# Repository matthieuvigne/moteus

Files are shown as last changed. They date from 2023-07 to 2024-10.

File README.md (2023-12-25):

# nautilus - a fork for moteus brushless servo driver

`nautilus` is a direct fork of moteus's driver with modified shape and interface to fit inside MyActuator's RMDX motors
(Mini-Cheatah like design), as a replacement of their driver. The main modifications are:

 - use an SPI interface instead of CAN
 - secondary SPI port for external encoder
 - usage of the `CSD88599` half-bridges instead of individual MOSFET to reduce the number of components
 - modified board shape and layout to fit inside the motor
 - the design is done using KiCad instead of Eagle

All new files are in the `nautilus` folder.

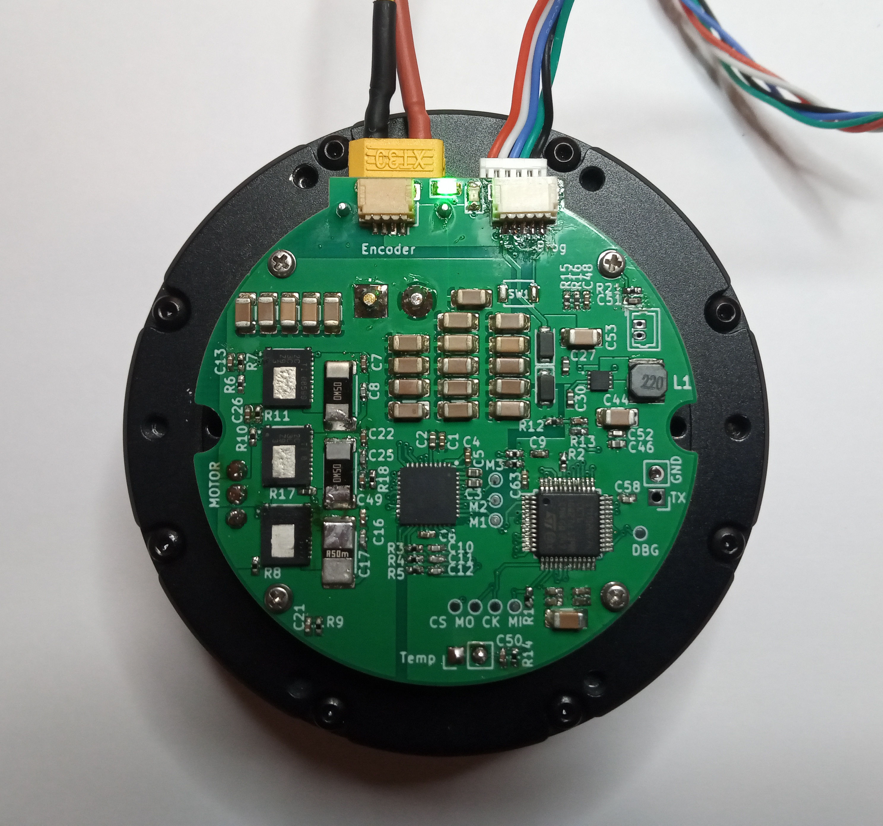
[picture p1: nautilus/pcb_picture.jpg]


# moteus brushless servo #

This contains full designs for the moteus brushless servo actuator,
including firmware and PCBs.

**WARNING**: This is not just a software project.  It includes designs
for moderately high power electronics.  It has not yet burned down my
(or anyone's that I know of) house, but there are no guarantees.

# Specifications #

| Name | Value |
|---|---|
| Voltage Input | 10-44V |
| Peak Electrical Power | 500W |
| Mass | 14.2g |
| Control Rate | 15-40kHz |
| PWM Switching Rate | 15-60kHz |
| CPU | 170Mhz STM32G4 |
| Peak phase current | 100A |
| Communications | 5Mbps CAN-FD |
| Dimensions | 46x53mm |

Assembled and tested boards can be purchased at https://mjbots.com/products/moteus-r4-11

# Directory structure #

* hw/ - hardware (mechanical and electrical designs)
  * controller/ - PCB design for servo controller
* fw/ - firmware for brushless controller
* lib/ - client side software
* utils/ - diagnostic tools
* tools/ - bazel build configure
* docs/ - documentation

# Documentation #

* [Getting Started](docs/getting_started.md)
* [Reference](docs/reference.md)

# Misc #

 * travis-ci 

# How to support moteus development #

The easiest way to support development the moteus hardware and firmware is as follows:

1) Buy things from https://mjbots.com
2) Build awesome machines!

That's it!  If for some reason you want to go above and beyond, you can sponsor mjbots through github: https://github.com/sponsors/mjbots

# License #

All files contained in this repository, unless otherwise noted, are
available under an Apache 2.0 License:
https://www.apache.org/licenses/LICENSE-2.0

# Trademark #

mjbots Robotic Systems LLC owns and protects the "mjbots" and "moteus" trademarks in many jurisdictions.

If you want to use these names in your project or product, please read the [Trademark Policy](https://mjbots.com/trademark-policy)

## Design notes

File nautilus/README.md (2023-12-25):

# How to compile and flash the firmware

## Installing dependencies

```sudo dnf install patch openocd arm-none-eabi-binutils-cs```

## Building the firmware

The firmware can be built by the following command:

```./tools/bazel test --config=target //fw:nautilus```

The bootloader also needs to be built (typically only once):

```./tools/bazel test --config=target //fw:can_bootloader ```

## Flashing

## Setting STM32 option bytes

Pin PB8 (boot) is used for I2C, thus pulled up. Hence, for the firmware to start running, the STM32 option bytes must be changed. This requires the software STM32CubeProgrammer, and the following configuration: nSWBOOT0 unchecked, nBOOT0 checked.

## Flashing

Simply run the python script: `python fw/flash.py`

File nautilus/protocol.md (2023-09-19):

# Nautilus motor driver protocol

Communication with the `nautilus` board is done using SPI. A fixed-size frame of 8 bytes is required for a complete transaction:

Input frame:
 - Byte 0: command byte 0
 - Byte 1: command byte 1 (typically register address)
 - Byte 2-5: data
 - Byte 6: unused
 - Byte 7: checksum

Output frame:
 - Byte 0-1: secondary encoder reading (14LSB) ; MSB 1 indicates a valid reading (Diagnostic register = 1)
 - Byte 2: current working mode
 - Byte 3-6: data
 - Byte 7: checksum

The checksum is simply the sum of the previous 6 bytes of the message.

**Note: for now, `nautilus` only supports SPI mode 1.**

## Available commands

### 0x01 <reg>: Register write

Write data to the register <reg>. If the register is non-writable, this has no effect

### 0x02 <reg>: Register read

Read data from register <reg>.

## 0x03: Perform commutation

For encoder commutation: enter voltage FOC mode:
 - next 4 bytes: float32_t, phase angle (0-1)
 - bytes 4-5: uint16_t, voltage amplitude as a fraction of maximum voltage

## 0x04 0x00: Store calibration results

Store the calibration result into persistent memory.

 - data[0-1]: uint16, encoder zero position
 - data[2]: uint8, encoder direction

## 0x05 0x00: Stop motor

## Register list

Address | Name                        | R/W | Persistent ? | Data type | Description
------- | ------------------          | --- | ------------ | --------- | -----------
0x00    | Current mode                | RO  | No           | uint8_t   | Current working mode, see details below
0x01    | Fault code                  | RO  | No           | uint32_t  | Fault error code

0x10    | Measured position           | RO  | No           | float32_t | Measured position, rad
0x11    | Measured speed              | RO  | No           | float32_t | Measured speed, rad/s
0x12    | Measured quadrature current | RO  | No           | float32_t | Measured quadrature current, A
0x13    | Measured current in phase A | RO  | No           | float32_t | Measured current in phase A, A
0x14    | Measured current in phase B | RO  | No           | float32_t | Measured current in phase B, A
0x15    | Measured current in phase C | RO  | No           | float32_t | Measured current in phase C, A
0x16    | Measured voltage in phase A | RO  | No           | float32_t | Measured voltage in phase A, V
0x17    | Measured voltage in phase B | RO  | No           | float32_t | Measured voltage in phase B, V
0x18    | Measured voltage in phase C | RO  | No           | float32_t | Measured voltage in phase C, V
0x19    | Measured motor temperature  | RO  | No           | float32_t | Measured motor temperature, C
0x1A    | Measured mosfet temperature | RO  | No           | float32_t | Measured mosfet temperature, C
0x1B    | Measured battery voltage    | RO  | No           | float32_t | Battery voltage, V

0x20    | Target position             | RW  | No           | float32_t | Target position, rad - also enter position mode
0x21    | Target speed                | RW  | No           | float32_t | Target speed, rad/s - also enter velocity mode
0x22    | Target quadrature current   | RW  | No           | float32_t | Target quadrature current, A - also enter current mode

0x30    | Raw encoder position        | RO  | No           | uint16_t | Raw encoder position, ticks
0x31    | Encoder orientation         | RW  | Yes          | uint8_t  | Encoder orientation with respect to motor
0x33    | Commutation offset          | RW  | Yes          | uint16_t | Commutation offset, ticks

0x40    | Current loop Kp             | RW  | Yes          | float32_t | Current loop Kp, V/A
0x41    | Current loop Ki             | RW  | Yes          | float32_t | Current loop Ki, Vs/A
0x42    | Current loop max integral   | RW  | Yes          | float32_t | Current loop max integral value, V

0x43    | Velocity loop Kp            | RW  | Yes          | float32_t | Velocity loop Kp, A/rad/s
0x44    | Velocity loop Ki            | RW  | Yes          | float32_t | Velocity loop Ki, As/rad/s
0x45    | Velocity loop max integral  | RW  | Yes          | float32_t | Velocity loop max integral value, A

0x50    | Motor max current           | RW  | Yes          | float32_t | Maximum motor current, A
0x51    | Motor max temperature       | RW  | Yes          | float32_t | Maximum motor temperature, deg C
0x52    | Mosfet max temperature      | RW  | Yes          | float32_t | Maximum mosfet temperature, deg C
0x53    | Communication timeout delay | RW  | Yes          | float32_t  | Communication timeout, s

## Register details

### 0x00: Current mode

Same as moteus:

    0 => stopped = writeable, clears faults
    1 => fault
    2,3,4 => preparing to operate
    5 => PWM mode
    6 => voltage mode
    7 => voltage FOC
    8 => voltage DQ
    9 => current
    10 => position
    11 => timeout
    12 => zero velocity
    13 => stay within
    14 => measure inductance
    15 => brake

 ### 0x01: Last error

Same as moteus 0x00f - fault code

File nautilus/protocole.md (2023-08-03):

# Nautilus motor driver protocole

Communication with the `nautilus` board is done using SPI. A fixed-size frame of 8 bytes is required for a
complete transaction:

Input frame:
 - Byte 0: command byte 0
 - Byte 1: command byte 1 (typically register address)
 - Byte 2-5: data
 - Byte 6: unused
 - Byte 7: checksum

Output frame:
 - Byte 0-1: secondary encoder reading
 - Byte 2: status byte
 - Byte 3-6: data
 - Byte 7: checksum

The checksum is simply the sum of the previous 6 bytes of the message.

## Available commands

### 0x01 <reg>: Register write

Write data to the register <reg>. If the register is non-writable, this has no effect

### 0x02 <reg>: Register read

Read data from register <reg>.

## 0x03 0x00: Perform calibration

Enter calibration mode: in voltage FOC, perform a full sweep of an electrical phase at the specified
velocity and power.

 - data[0-1]: uint16, duration of the sweep in ms.
 - data[2-3]: uint16, amplitude of the voltage in steps of 0.1%

## 0x03 0x01: Store calibration results

Store the calibration result into persistent memory.

## Register list

Address | Name                        | R/W | Persistent ? | Data type | Description
------- | ------------------          | --- | ------------ | --------- | -----------
0x00    | Current mode                | RW  | No           | uint32_t  | Current working mode, see details below
0x01    | Last error                  | RO  | No           | uint32_t  | Last error to have occured

0x10    | Measured position           | RO  | No           | float32_t | Measured position, rad
0x11    | Measured speed              | RO  | No           | float32_t | Measured speed, rad/s
0x12    | Measured quadrature current | RO  | No           | float32_t | Measured quadrature current, A
0x13    | Measured current in phase A | RO  | No           | float32_t | Measured current in phase A, A
0x14    | Measured current in phase B | RO  | No           | float32_t | Measured current in phase B, A
0x15    | Measured current in phase C | RO  | No           | float32_t | Measured current in phase C, A
0x16    | Measured voltage in phase A | RO  | No           | float32_t | Measured voltage in phase A, V
0x17    | Measured voltage in phase B | RO  | No           | float32_t | Measured voltage in phase B, V
0x18    | Measured voltage in phase C | RO  | No           | float32_t | Measured voltage in phase C, V
0x19    | Measured motor temperature  | RO  | No           | float32_t | Measured motor temperature, C
0x1A    | Measured mosfet temperature | RO  | No           | float32_t | Measured mosfet temperature, C
0x1B    | Measured battery voltage    | RO  | No           | float32_t | Battery voltage, V

0x20    | Target position             | RW  | No           | float32_t | Target position, rad
0x21    | Target speed                | RW  | No           | float32_t | Target speed, rad/s
0x22    | Target quadrature current   | RW  | No           | float32_t | Target quadrature current, A

0x30    | Raw encoder position        | RO  | No           | uint16_t | Raw encoder position, ticks
0x31    | Encoder orientation         | RW  | Yes          | uint8_t  | Encoder orientation with respect to motor
0x33    | Commutation offset          | RW  | Yes          | uint16_t | Commutation offset, ticks

0x40    | Current loop Kp             | RW  | Yes          | float32_t | Current loop Kp, V/A
0x41    | Current loop Ki             | RW  | Yes          | float32_t | Current loop Ki, Vs/A
0x42    | Current loop max integral   | RW  | Yes          | float32_t | Current loop max integral value, V

0x43    | Velocity loop Kp            | RW  | Yes          | float32_t | Velocity loop Kp, A/rad/s
0x44    | Velocity loop Ki            | RW  | Yes          | float32_t | Velocity loop Ki, As/rad/s
0x45    | Velocity loop max integral  | RW  | Yes          | float32_t | Velocity loop max integral value, A

0x50    | Motor max current           | RW  | Yes          | float32_t | Maximum motor current, A
0x51    | Motor max temperature       | RW  | Yes          | float32_t | Maximum motor temperature, deg C
0x52    | Mosfet max temperature      | RW  | Yes          | float32_t | Maximum mosfet temperature, deg C
0x53    | Communication timeout delay | RW  | Yes          | uint16_t  | Communication timeout limit, ms

## Register details

### 0x00: Current mode

List mode of operations:

 - 0x00: power off
 - 0x01: brake
 - 0x02: voltage FOC (commutation)
 - 0x03: current mode
 - 0x04: velocity mode

 ### 0x01: Last error

 List of errors: TODO

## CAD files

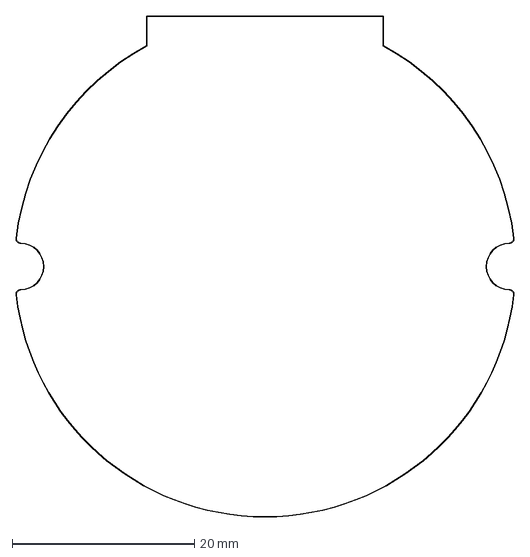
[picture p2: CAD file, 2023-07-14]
nautilus/hw/outline.dxf
54.7 x 55.0 mm

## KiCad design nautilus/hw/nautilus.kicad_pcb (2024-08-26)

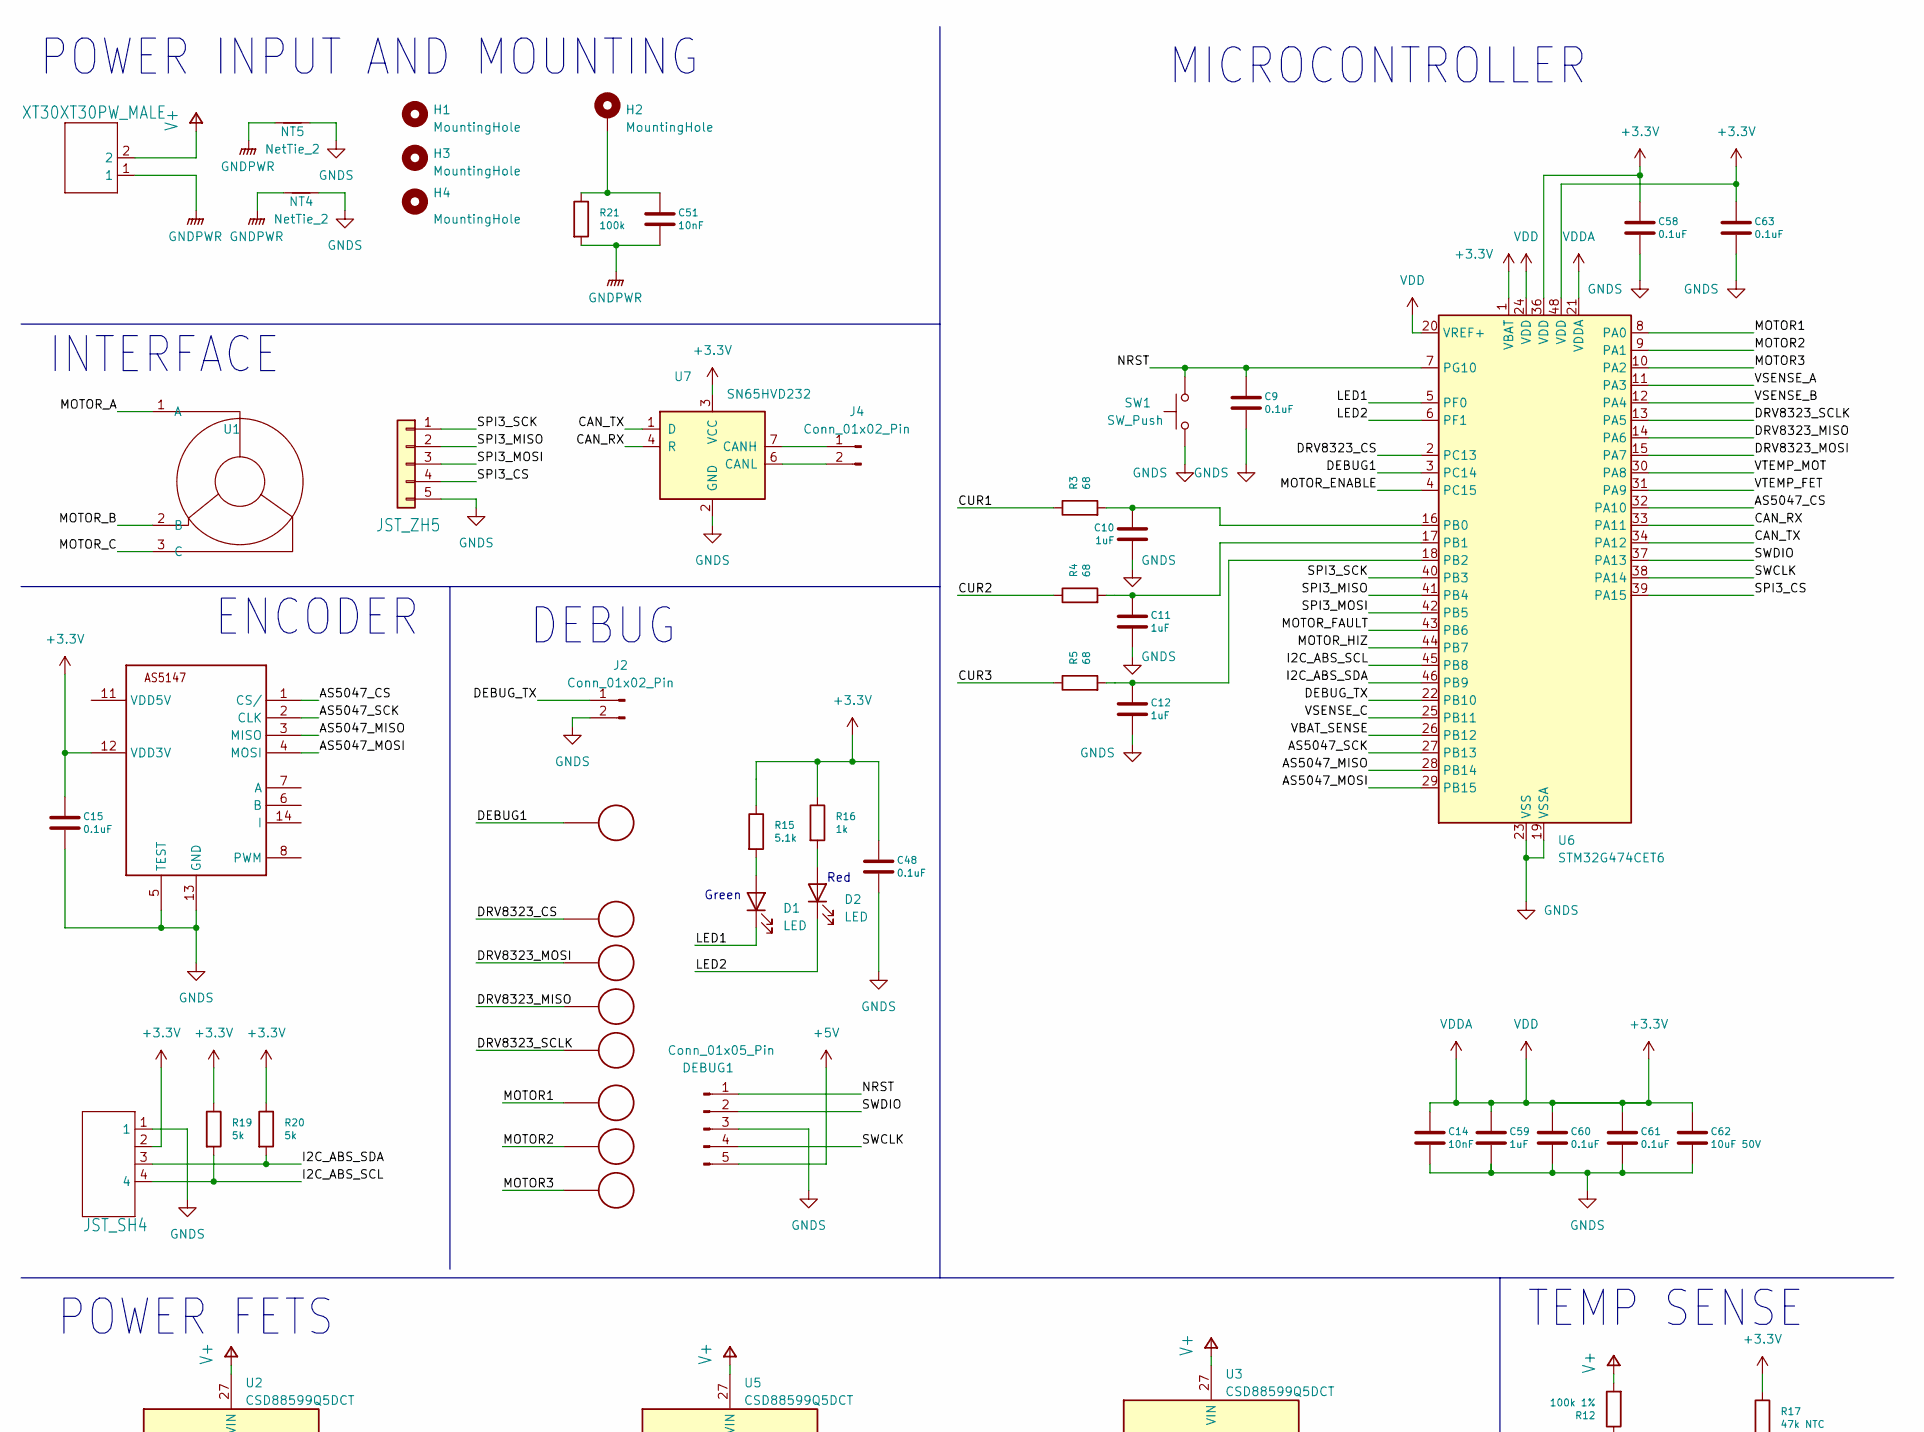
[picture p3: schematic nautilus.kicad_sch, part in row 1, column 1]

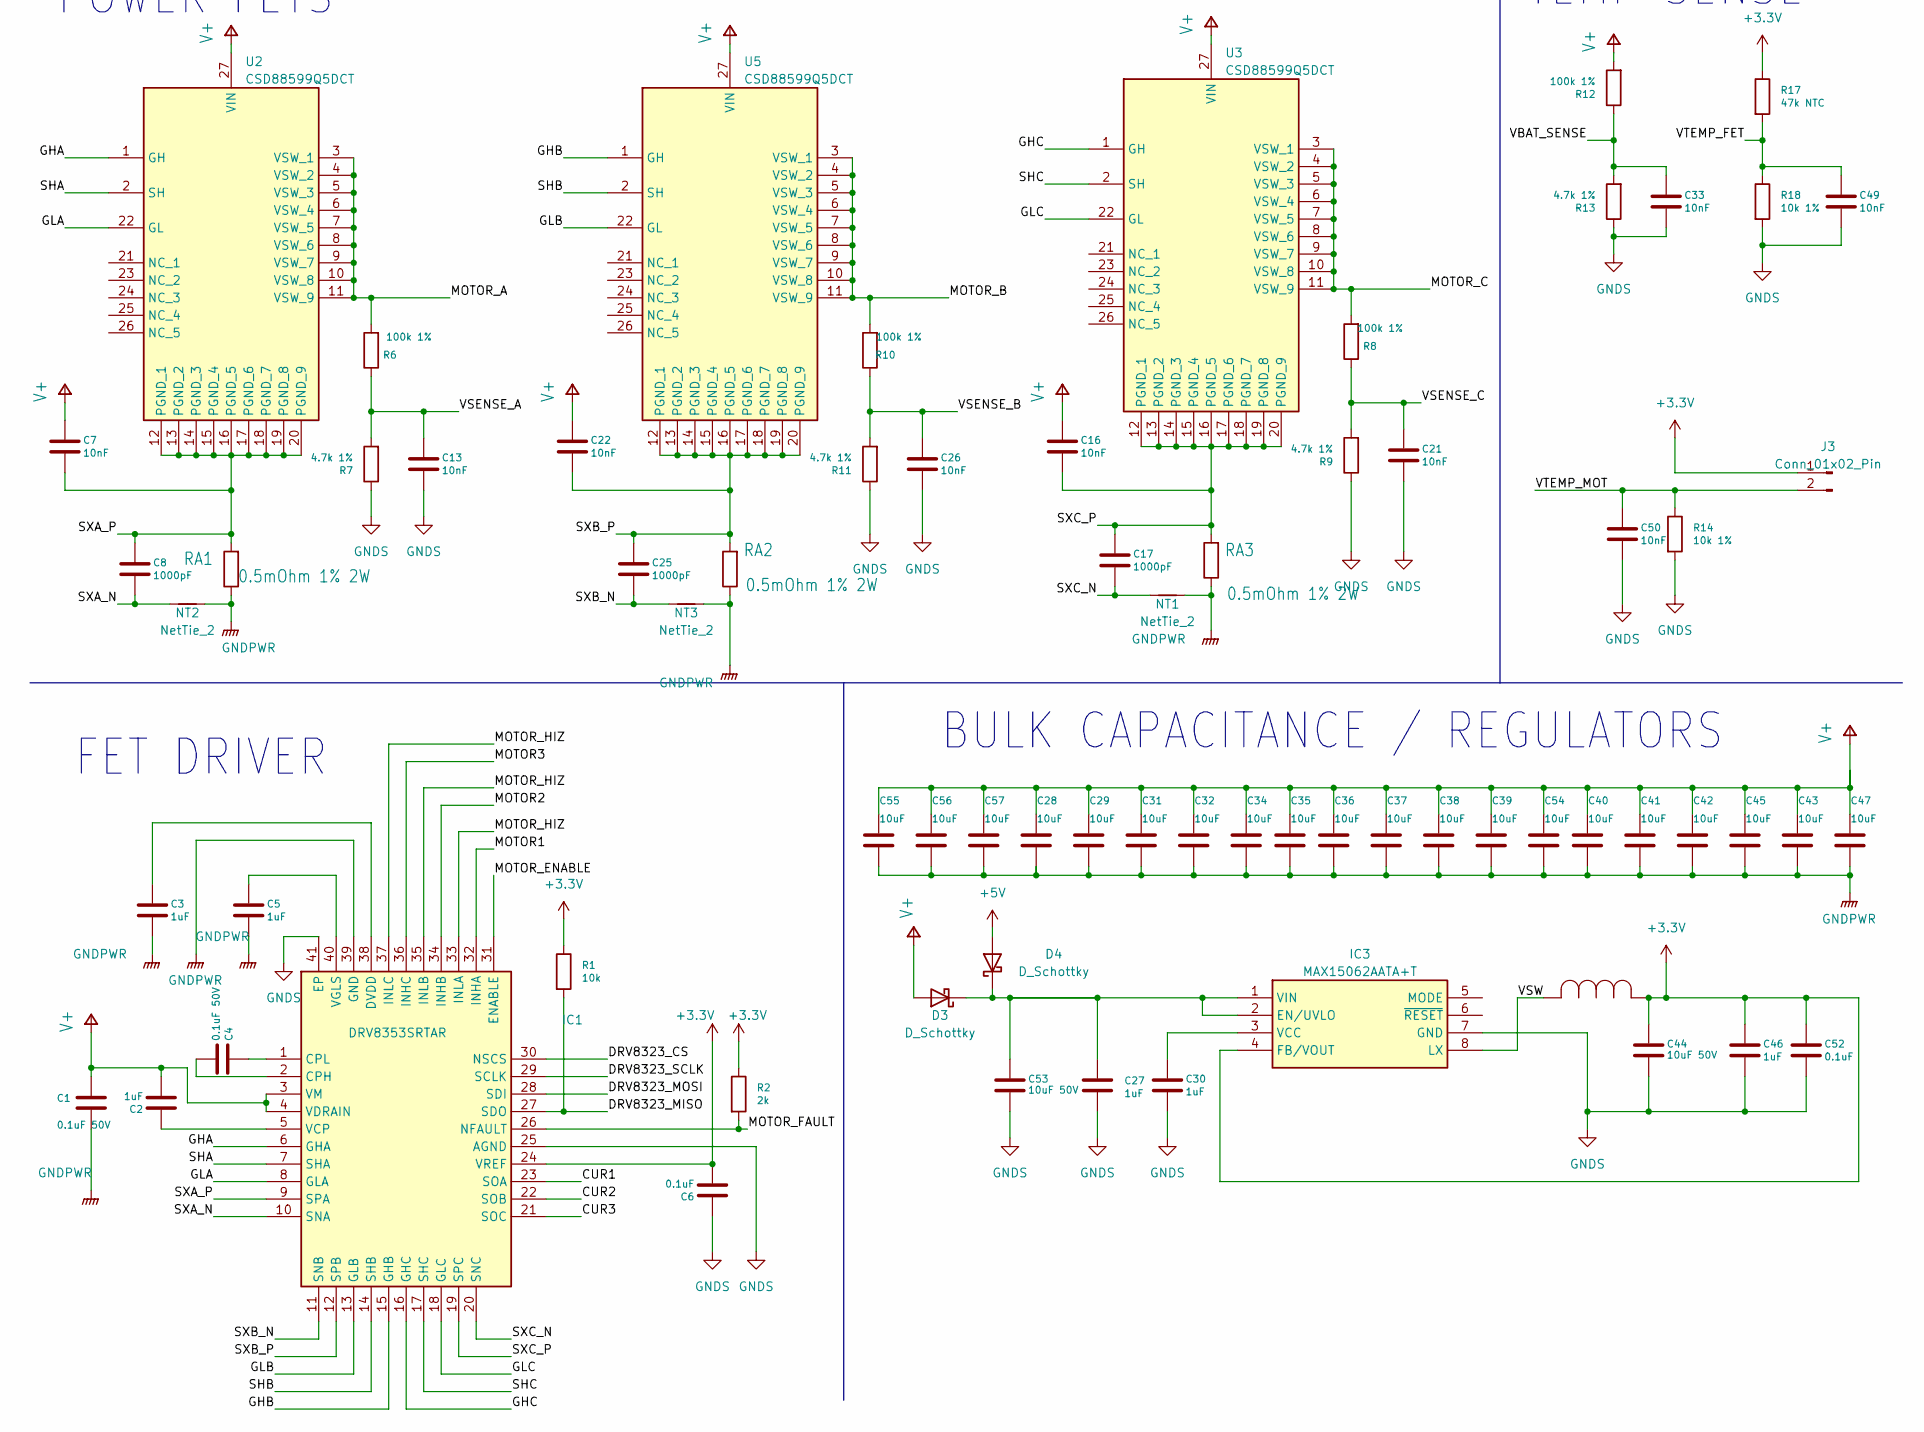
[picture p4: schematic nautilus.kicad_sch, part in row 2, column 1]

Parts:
C1, C4: 0.1uF 50V; C_0402_1005Metric_Pad0.74x0.62mm_HandSolder; MPN CGA2B3X7R1H104K050BB
C2, C3, C5, C46, C59: 1uF; C_0402_1005Metric_Pad0.74x0.62mm_HandSolder; MPN MF-CAP-0402-1uF
C6, C9, C15, C48, C52, C58, C60, C61, C63: 0.1uF; C_0402_1005Metric_Pad0.74x0.62mm_HandSolder; MPN MF-CAP-0402-0.1uF
C7, C13, C14, C16, C21, C22, C26, C51: 10nF; C_0402_1005Metric_Pad0.74x0.62mm_HandSolder; MPN MF-CAP-0402-1nF
C8, C17, C25: 1000pF; C_0402_1005Metric_Pad0.74x0.62mm_HandSolder; MPN MF-CAP-0402-1nF
C10, C11, C12: 1uF; C_0402_1005Metric_Pad0.74x0.62mm_HandSolder; MPN MF-CAP-0402-1nF
C27, C30: 1uF; C_0402_1005Metric_Pad0.74x0.62mm_HandSolder; MPN MF-CAP-0603-1uF
C28, C29, C31, C32, C34, C35, C36, C37, C38, C39, C40, C41, C42, C43, C45, C47, C54, C55, C56, C57: 10uF; C_1206_3216Metric_Pad1.33x1.80mm_HandSolder; MPN CL31A106MBHNNNE; Mouser Part Number 187-CL31A106MBHNNNE
C33, C50: 10nF; C_0402_1005Metric_Pad0.74x0.62mm_HandSolder; MPN MF-CAP-0402-0.01uF
C44, C53, C62: 10uF 50V; C_1206_3216Metric_Pad1.33x1.80mm_HandSolder; MPN CL31A106MBHNNNE; Mouser Part Number 187-CL31A106MBHNNNE
C49: 10nF; C_0402_1005Metric_Pad0.74x0.62mm_HandSolder; MPN MF-CAP-0402-0.1uF
D1, D2: LED; LED_0805_2012Metric_Pad1.15x1.40mm_HandSolder
D3, D4: D_Schottky; D_SOD-123F; Mouser Part Number 833-SMD210PLQ-TP
DBG1: PAD24AWG_PAD; TestPoint_Pad_D1.0mm
DEBUG1: Conn_01x05_Pin; JST_SH_SM05B-SRSS-TB_1x05-1MP_P1.00mm_Horizontal
DRV_CS1: PAD24AWG_PAD; TestPoint_Pad_D1.0mm
DRV_MISO1: PAD24AWG_PAD; TestPoint_Pad_D1.0mm
DRV_MOSI1: PAD24AWG_PAD; TestPoint_Pad_D1.0mm
DRV_SCK1: PAD24AWG_PAD; TestPoint_Pad_D1.0mm
H1, H2, H3, H4: MountingHole; MountingHole-Plated
IC1: DRV8353SRTAR; QFN50P600X600X80-41N-D; Manufacturer_Part_Number DRV8353SRTAR; Mouser Part Number 595-DRV8353SRTAT
IC3: MAX15062AATA+T; MAX15062AATAT; Manufacturer_Part_Number MAX15062AATA+T; Mouser Part Number 700-MAX15062AATA+T
J1: XT30XT30PW_MALE; AMASS_XT30PW-M_1x02_P2.50mm_Horizontal
J2, J3: Conn_01x02_Pin; PinHeader_1x02_P2.54mm_Vertical
J4: Conn_01x02_Pin; Molex_PicoBlade_53047-0210_1x02_P1.25mm_Vertical
L1: SRN4018-220M; SRN4018220M; MANUFACTURER_PART_NUMBER SRN4018-330M; Mouser SRN4018
M1, M2, M3: PAD24AWG_PAD; TestPoint_Pad_D1.0mm
NT1, NT2, NT3, NT4, NT5: NetTie_2; NetTie-2_SMD_Pad0.5mm
R1: 10k; R_0402_1005Metric_Pad0.72x0.64mm_HandSolder; MPN MF-RES-0402-2K
R2: 2k; R_0402_1005Metric_Pad0.72x0.64mm_HandSolder; MPN MF-RES-0402-2K
R3, R4, R5: 68; R_0402_1005Metric_Pad0.72x0.64mm_HandSolder; MPN MF-RES-0402-22
R6, R8, R10, R12: 100k 1%; R_0402_1005Metric_Pad0.72x0.64mm_HandSolder; MPN RC0402FR-07100KL
R7, R9, R11, R13: 4.7k 1%; R_0402_1005Metric_Pad0.72x0.64mm_HandSolder; MPN RC0402FR-074K7L
R14, R18: 10k 1%; R_0402_1005Metric_Pad0.72x0.64mm_HandSolder; MPN RC0402FR-0710KL
R15: 5.1k; R_0402_1005Metric_Pad0.72x0.64mm_HandSolder; MPN MF-RES-0402-560
R16: 1k; R_0402_1005Metric_Pad0.72x0.64mm_HandSolder; MPN MF-RES-0402-560
R17: 47k NTC; R_0402_1005Metric_Pad0.72x0.64mm_HandSolder; MPN NCP15WB473F03RC; Mouser Part Number 81-NCP15WB473F03RC
R19, R20: 5k; R_0402_1005Metric_Pad0.72x0.64mm_HandSolder; MPN MF-RES-0402-2K
R21: 100k; R_0402_1005Metric_Pad0.72x0.64mm_HandSolder; MPN MF-RES-0402-2K
RA1, RA2, RA3: 0.5mOhm 1% 2W; R_2512_6332Metric_Pad1.40x3.35mm_HandSolder; MPN HCS1206FTL500; Mouser 504-MSMA2512R0005FGM
SPI1: JST_ZH5; JST_GH_SM05B-GHS-TB_1x05-1MP_P1.25mm_Horizontal; MPN S4B-ZR-SM4A-TF(LF)(SN)
SPI2: JST_SH4; JST_SH_SM04B-SRSS-TB_1x04-1MP_P1.00mm_Horizontal; MPN S4B-ZR-SM4A-TF(LF)(SN)
SW1: SW_Push; SW_SPST_B3U-1000P
U1: BrushlessMotor
U2, U3, U5: CSD88599Q5DCT; Q5DC_DMM; Manufacturer_Part_Number CSD88599Q5DCT; Mouser Part Number 595-CSD88599Q5DCT
U4: AS5147; TSSOP-14_4.4x5mm_P0.65mm; MPN AS5047P-ATSM
U6: STM32G474CET6; LQFP-48_7x7mm_P0.5mm; Mouser Part Number 511-STM32G474CET6
U7: SN65HVD232; SOIC-8_3.9x4.9mm_P1.27mm

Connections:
+3.3V: C6.2, C14.1, C15.1, C44.1, C46.1, C48.1, C52.1, C58.1, C59.1, C60.1, C61.1, C62.1, C63.1, IC1.24 (VREF), IC3.4 (FB/VOUT), J3.1, L1.1, R1.1, R2.1, R15.1, R16.1, R17.1, R19.1, R20.1, SPI2.2, U4.12 (VDD3V), U6.1 (VBAT), U6.20 (VREF+), U6.21 (VDDA), U6.24 (VDD), U6.36 (VDD), U6.48 (VDD), U7.3 (VCC)
+5V: D4.2 (A), DEBUG1.5
/AS5047_CS: U4.1 (CS/), U6.32 (PA10)
/AS5047_MISO: U4.3 (MISO), U6.28 (PB14)
/AS5047_MOSI: U4.4 (MOSI), U6.29 (PB15)
/AS5047_SCK: U4.2 (CLK), U6.27 (PB13)
/CAN_RX: U6.33 (PA11), U7.4 (R)
/CAN_TX: U6.34 (PA12), U7.1 (D)
/CUR1: IC1.23 (SOA), R3.1
/CUR2: IC1.22 (SOB), R4.1
/CUR3: IC1.21 (SOC), R5.1
/DEBUG1: DBG1.1, U6.3 (PC14)
/DEBUG_TX: J2.1, U6.22 (PB10)
/DRV8323_CS: DRV_CS1.1, IC1.30 (NSCS), U6.2 (PC13)
/DRV8323_MISO: DRV_MISO1.1, IC1.27 (SDO), R1.2, U6.14 (PA6)
/DRV8323_MOSI: DRV_MOSI1.1, IC1.28 (SDI), U6.15 (PA7)
/DRV8323_SCLK: DRV_SCK1.1, IC1.29 (SCLK), U6.13 (PA5)
/GHA: IC1.6 (GHA), U2.1 (GH)
/GHB: IC1.15 (GHB), U5.1 (GH)
/GHC: IC1.16 (GHC), U3.1 (GH)
/GLA: IC1.8 (GLA), U2.22 (GL)
/GLB: IC1.13 (GLB), U5.22 (GL)
/GLC: IC1.18 (GLC), U3.22 (GL)
/I2C_ABS_SCL: R19.2, SPI2.4, U6.45 (PB8)
/I2C_ABS_SDA: R20.2, SPI2.3, U6.46 (PB9)
/LED1: D1.1 (K), U6.5 (PF0)
/LED2: D2.1 (K), U6.6 (PF1)
/MOTOR1: IC1.32 (INHA), M1.1, U6.8 (PA0)
/MOTOR2: IC1.34 (INHB), M2.1, U6.9 (PA1)
/MOTOR3: IC1.36 (INHC), M3.1, U6.10 (PA2)
/MOTOR_A: R6.2, U1.1 (A), U2.3 (VSW_1), U2.4 (VSW_2), U2.5 (VSW_3), U2.6 (VSW_4), U2.7 (VSW_5), U2.8 (VSW_6), U2.9 (VSW_7), U2.10 (VSW_8), U2.11 (VSW_9)
/MOTOR_B: R10.2, U1.2 (B), U5.3 (VSW_1), U5.4 (VSW_2), U5.5 (VSW_3), U5.6 (VSW_4), U5.7 (VSW_5), U5.8 (VSW_6), U5.9 (VSW_7), U5.10 (VSW_8), U5.11 (VSW_9)
/MOTOR_C: R8.2, U1.3 (C), U3.3 (VSW_1), U3.4 (VSW_2), U3.5 (VSW_3), U3.6 (VSW_4), U3.7 (VSW_5), U3.8 (VSW_6), U3.9 (VSW_7), U3.10 (VSW_8), U3.11 (VSW_9)
/MOTOR_ENABLE: IC1.31 (ENABLE), U6.4 (PC15)
/MOTOR_FAULT: IC1.26 (NFAULT), R2.2, U6.43 (PB6)
/MOTOR_HIZ: IC1.33 (INLA), IC1.35 (INLB), IC1.37 (INLC), U6.44 (PB7)
/NRST: C9.1, DEBUG1.1, SW1.2, U6.7 (PG10)
/SHA: IC1.7 (SHA), U2.2 (SH)
/SHB: IC1.14 (SHB), U5.2 (SH)
/SHC: IC1.17 (SHC), U3.2 (SH)
/SPI3_CS: SPI1.4, U6.39 (PA15)
/SPI3_MISO: SPI1.2, U6.41 (PB4)
/SPI3_MOSI: SPI1.3, U6.42 (PB5)
/SPI3_SCK: SPI1.1, U6.40 (PB3)
/SWCLK: DEBUG1.4, U6.38 (PA14)
/SWDIO: DEBUG1.2, U6.37 (PA13)
/SXA_N: C8.2, IC1.10 (SNA), NT2.2
/SXA_P: C7.2, C8.1, IC1.9 (SPA), RA1.2, U2.12 (PGND_1), U2.13 (PGND_2), U2.14 (PGND_3), U2.15 (PGND_4), U2.16 (PGND_5), U2.17 (PGND_6), U2.18 (PGND_7), U2.19 (PGND_8), U2.20 (PGND_9)
/SXB_N: C25.2, IC1.11 (SNB), NT3.2
/SXB_P: C22.2, C25.1, IC1.12 (SPB), RA2.2, U5.12 (PGND_1), U5.13 (PGND_2), U5.14 (PGND_3), U5.15 (PGND_4), U5.16 (PGND_5), U5.17 (PGND_6), U5.18 (PGND_7), U5.19 (PGND_8), U5.20 (PGND_9)
/SXC_N: C17.2, IC1.20 (SNC), NT1.2
/SXC_P: C16.2, C17.1, IC1.19 (SPC), RA3.2, U3.12 (PGND_1), U3.13 (PGND_2), U3.14 (PGND_3), U3.15 (PGND_4), U3.16 (PGND_5), U3.17 (PGND_6), U3.18 (PGND_7), U3.19 (PGND_8), U3.20 (PGND_9)
/VBAT_SENSE: C33.1, R12.1, R13.2, U6.26 (PB12)
/VSENSE_A: C13.1, R6.1, R7.2, U6.11 (PA3)
/VSENSE_B: C26.1, R10.1, R11.2, U6.12 (PA4)
/VSENSE_C: C21.1, R8.1, R9.2, U6.25 (PB11)
/VSW: IC3.8 (LX), L1.2
/VTEMP_FET: C49.1, R17.2, R18.1, U6.31 (PA9)
/VTEMP_MOT: C50.1, J3.2, R14.1, U6.30 (PA8)
GNDPWR: C1.2, C3.2, C5.2, C28.2, C29.2, C31.2, C32.2, C34.2, C35.2, C36.2, C37.2, C38.2, C39.2, C40.2, C41.2, C42.2, C43.2, C45.2, C47.2, C51.2, C54.2, C55.2, C56.2, C57.2, IC1.39 (GND), J1.1, NT1.1, NT2.1, NT3.1, NT4.2, NT5.2, R21.2, RA1.1, RA2.1, RA3.1
GNDS: C6.1, C9.2, C10.2, C11.2, C12.2, C13.2, C14.2, C15.2, C21.2, C26.2, C27.2, C30.2, C33.2, C44.2, C46.2, C48.2, C49.2, C50.2, C52.2, C53.2, C58.2, C59.2, C60.2, C61.2, C62.2, C63.2, DEBUG1.3, IC1.25 (AGND), IC1.41 (EP), IC3.7 (GND), J2.2, NT4.1, NT5.1, R7.1, R9.1, R11.1, R13.1, R14.2, R18.2, SPI1.5, SPI2.1, SW1.1, U4.5 (TEST), U4.13 (GND), U6.19 (VSSA), U6.23 (VSS), U6.35 (VSS), U6.47 (VSS), U7.2 (GND)
unnamed: C51.1, H2.1, R21.1
unnamed: D1.2 (A), R15.2
unnamed: D2.2 (A), R16.2
unnamed: C27.1, C53.1, D3.1 (K), D4.1 (K), IC3.1 (VIN), IC3.2 (EN/UVLO)
unnamed: C4.2, IC1.2 (CPH)
unnamed: C4.1, IC1.1 (CPL)
unnamed: C3.1, IC1.38 (DVDD)
unnamed: C2.1, IC1.5 (VCP)
unnamed: C5.1, IC1.40 (VGLS)
unnamed: C30.1, IC3.3 (VCC)
unnamed: J4.1, U7.7 (CANH)
unnamed: J4.2, U7.6 (CANL)
unnamed: C10.1, R3.2, U6.16 (PB0)
unnamed: C11.1, R4.2, U6.17 (PB1)
unnamed: C12.1, R5.2, U6.18 (PB2)
V+: C1.1, C2.2, C7.1, C16.1, C22.1, C28.1, C29.1, C31.1, C32.1, C34.1, C35.1, C36.1, C37.1, C38.1, C39.1, C40.1, C41.1, C42.1, C43.1, C45.1, C47.1, C54.1, C55.1, C56.1, C57.1, D3.2 (A), IC1.3 (VM), IC1.4 (VDRAIN), J1.2, R12.2, U2.27 (VIN), U3.27 (VIN), U5.27 (VIN)

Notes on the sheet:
Green
INTERFACE
POWER INPUT AND MOUNTING
TEMP SENSE
ENCODER
Red
MICROCONTROLLER
FET DRIVER
BULK CAPACITANCE / REGULATORS
DEBUG
POWER FETS

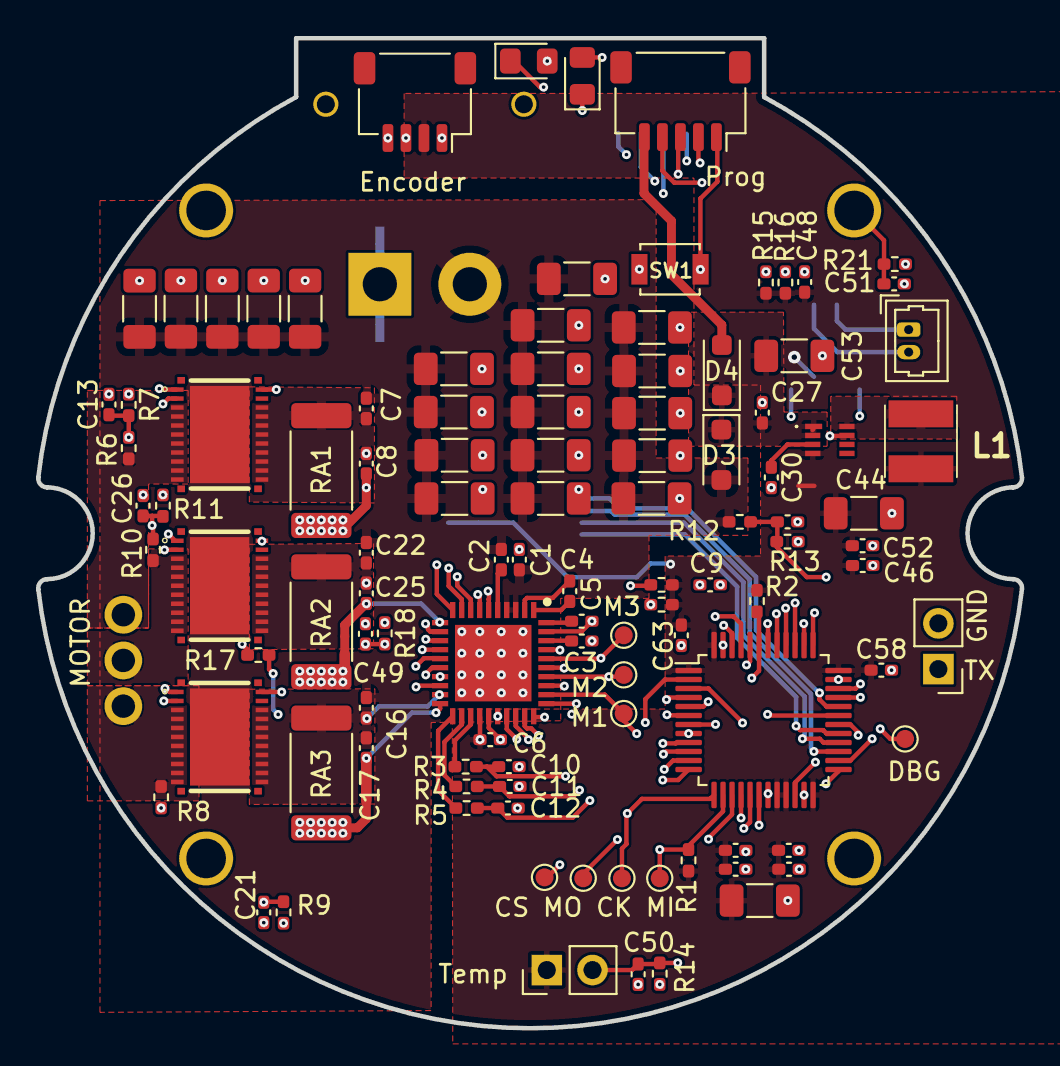
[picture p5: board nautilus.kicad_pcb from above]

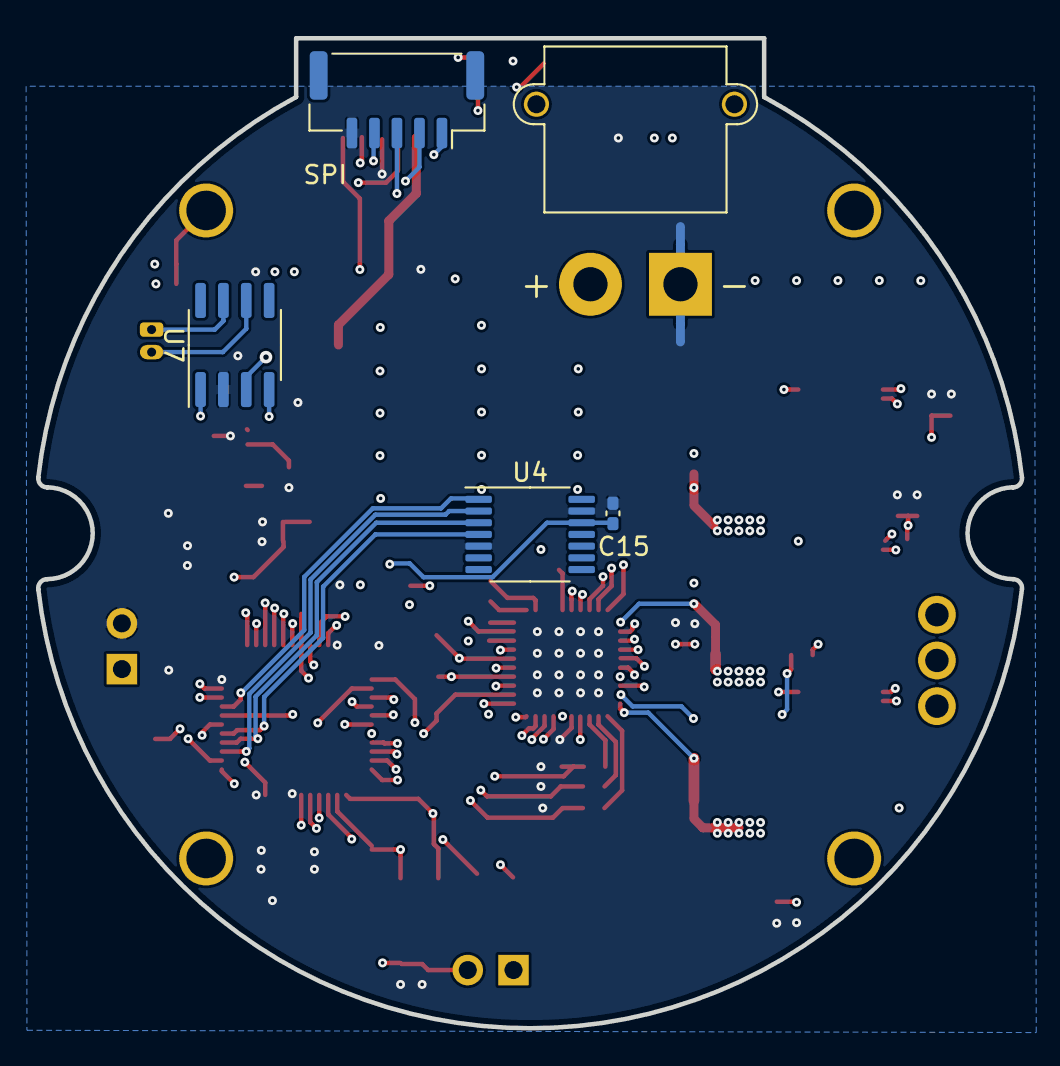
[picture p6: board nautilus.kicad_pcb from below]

Board: 4 copper layers, 54.7 x 55.0 mm, 121 parts (7 on the bottom side), 77 nets.

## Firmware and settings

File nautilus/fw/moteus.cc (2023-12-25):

// Copyright 2018-2022 Josh Pieper, jjp@pobox.com.
//
// Licensed under the Apache License, Version 2.0 (the "License");
// you may not use this file except in compliance with the License.
// You may obtain a copy of the License at
//
//     http://www.apache.org/licenses/LICENSE-2.0
//
// Unless required by applicable law or agreed to in writing, software
// distributed under the License is distributed on an "AS IS" BASIS,
// WITHOUT WARRANTIES OR CONDITIONS OF ANY KIND, either express or implied.
// See the License for the specific language governing permissions and
// limitations under the License.

#include <inttypes.h>

#include <functional>

#include "mbed.h"

#include "mjlib/micro/async_exclusive.h"
#include "mjlib/micro/async_stream.h"
#include "mjlib/micro/command_manager.h"
#include "mjlib/micro/persistent_config.h"
#include "mjlib/micro/telemetry_manager.h"
#include "mjlib/micro/stream_pipe.h"
#include "mjlib/multiplex/micro_server.h"
#include "mjlib/multiplex/micro_stream_datagram.h"

#include "fw/board_debug.h"
#include "fw/clock_manager.h"
#include "fw/firmware_info.h"
#include "fw/git_info.h"
#include "fw/millisecond_timer.h"
#include "fw/moteus_controller.h"
#include "fw/moteus_hw.h"
#include "fw/system_info.h"
#include "fw/uuid.h"

#if defined(TARGET_STM32G4)
#include "fw/fdcan.h"
#include "fw/fdcan_micro_server.h"
#include "fw/stm32g4_async_uart.h"
#include "fw/stm32g4_flash.h"
#else
#error "Unknown target"
#endif

extern "C" {
  uint32_t kMoteusFirmwareVersion = MOTEUS_FIRMWARE_VERSION;
}

auto* const MyDWT = DWT;
auto* const MyFLASH = FLASH;

using namespace moteus;
namespace micro = mjlib::micro;
namespace multiplex = mjlib::multiplex;

#if defined(TARGET_STM32G4)
using HardwareUart = Stm32G4AsyncUart;
using Stm32Flash = Stm32G4Flash;
#else
#error "Unknown target"
#endif

extern "C" {
void SetupClock() {
#if defined(TARGET_STM32G4)
  {
    __HAL_RCC_SYSCFG_CLK_ENABLE();
    __HAL_RCC_PWR_CLK_ENABLE();

    RCC_ClkInitTypeDef RCC_ClkInitStruct;

    RCC_ClkInitStruct.ClockType      = (RCC_CLOCKTYPE_SYSCLK | RCC_CLOCKTYPE_HCLK | RCC_CLOCKTYPE_PCLK1 | RCC_CLOCKTYPE_PCLK2);
    RCC_ClkInitStruct.SYSCLKSource = RCC_SYSCLKSOURCE_PLLCLK;
    RCC_ClkInitStruct.AHBCLKDivider = RCC_SYSCLK_DIV1; // 170 MHz
    RCC_ClkInitStruct.APB1CLKDivider = RCC_HCLK_DIV2;  //  85 MHz
    RCC_ClkInitStruct.APB2CLKDivider = RCC_HCLK_DIV2;  //  85 MHz

    if (HAL_RCC_ClockConfig(&RCC_ClkInitStruct, FLASH_LATENCY_6) != HAL_OK) {
      mbed_die();
    }

    RCC_PeriphCLKInitTypeDef PeriphClkInit = {};

    PeriphClkInit.PeriphClockSelection =
        RCC_PERIPHCLK_FDCAN |
        RCC_PERIPHCLK_USART2 |
        RCC_PERIPHCLK_USART3 |
        RCC_PERIPHCLK_ADC12 |
        RCC_PERIPHCLK_ADC345 |
        RCC_PERIPHCLK_I2C1
        ;
    PeriphClkInit.FdcanClockSelection = RCC_FDCANCLKSOURCE_PCLK1;
    PeriphClkInit.Usart2ClockSelection = RCC_USART2CLKSOURCE_PCLK1;
    PeriphClkInit.Usart3ClockSelection = RCC_USART3CLKSOURCE_PCLK1;
    PeriphClkInit.Adc12ClockSelection = RCC_ADC12CLKSOURCE_SYSCLK;
    PeriphClkInit.Adc345ClockSelection = RCC_ADC345CLKSOURCE_SYSCLK;
    PeriphClkInit.I2c1ClockSelection = RCC_I2C1CLKSOURCE_SYSCLK;
    if (HAL_RCCEx_PeriphCLKConfig(&PeriphClkInit) != HAL_OK) {
      mbed_die();
    }

    __HAL_RCC_TIM2_CLK_ENABLE();
    __HAL_RCC_TIM3_CLK_ENABLE();
    __HAL_RCC_TIM4_CLK_ENABLE();
  }
#endif
}
}

#if defined(TARGET_STM32G4)
extern "C" {
extern char _sccmram;
extern char _siccmram;
extern char _eccmram;
extern char _sccmram;
}
#endif

namespace moteus {
volatile uint8_t g_measured_hw_family;
volatile uint8_t g_measured_hw_rev;
volatile uint8_t g_measured_hw_pins;
MoteusHwPins g_hw_pins;
}

namespace {
struct CanConfig {
  uint32_t prefix = 0;

  template <typename Archive>
  void Serialize(Archive* a) {
    a->Visit(MJ_NVP(prefix));
  }

  bool operator==(const CanConfig& rhs) const {
    return prefix == rhs.prefix;
  }
};
}

int main(void) {
#if defined(TARGET_STM32G4)
  std::memcpy(&_sccmram, &_siccmram, &_eccmram - &_sccmram);
#endif

  FLASH->ACR |= FLASH_ACR_PRFTEN | FLASH_ACR_ICEN | FLASH_ACR_DCEN;

#if 0
  // We map SRAM1 onto address 0 just to make finding accesses to
  // address 0 easier.
  SYSCFG->MEMRMP = (SYSCFG->MEMRMP & ~SYSCFG_MEMRMP_MEM_MODE_Msk) | 0x03;  // SRAM1
#endif

  SetupClock();

  // I initially used a Ticker here to enqueue events at 1ms
  // intervals.  However, it introduced jitter into the current
  // sampling interrupt, and I couldn't figure out how to get the
  // interrupt priorities right.  Thus for now we just poll to look
  // for millisecond turnover.
  MillisecondTimer timer;

  const auto family_and_version = DetectMoteusFamily(&timer);
  g_measured_hw_family = family_and_version.family;
  g_measured_hw_rev = family_and_version.hw_version;
  g_measured_hw_pins = family_and_version.hw_pins;

  g_hw_pins = FindHardwarePins(family_and_version);

  // We do our compatibility check *after* calling FindHardwarePins so
  // the the family specific pins are known.  That way mbed_die
  // doesn't choke being unable to find the power LED for instance.

  if (family_and_version.hw_version < 0) {
    // This firmware is not compatible with this board.
    mbed_die();
  }

  // We require cycle counting be enabled for some things.
  {
    ITM->LAR = 0xC5ACCE55;
    CoreDebug->DEMCR |= CoreDebug_DEMCR_TRCENA_Msk;
    DWT->CYCCNT = 0;
    DWT->CTRL |= DWT_CTRL_CYCCNTENA_Msk;
  }

  micro::SizedPool<20000> pool;

  std::optional<HardwareUart> rs485;
  if (g_hw_pins.uart_tx != NC) {
    rs485.emplace(&pool, &timer, []() {
      HardwareUart::Options options;
      options.tx = g_hw_pins.uart_tx;
      options.rx = g_hw_pins.uart_rx;
      options.dir = g_hw_pins.uart_dir;
      options.baud_rate = 1000000;
      return options;
                                 }());
  }

  FDCan fdcan([]() {
      FDCan::Options options;

      options.td = g_hw_pins.can_td;
      options.rd = g_hw_pins.can_rd;

      options.slow_bitrate = 1000000;
      options.fast_bitrate = 5000000;

      options.fdcan_frame = true;
      options.bitrate_switch = true;
      options.automatic_retransmission = true;

      // Family 0 uses a TCAN334GDCNT, which has a very low loop
      // delay.  Other families use chips with a longer loop delay.
      options.delay_compensation = g_measured_hw_family != 0;

      options.tdc_offset = 13;  // 13 / 85MHz ~= 152ns
      options.tdc_filter = 2; // 2 / 85MHz ~= 23ns

      return options;
    }());
  FDCanMicroServer fdcan_micro_server(&fdcan);
  multiplex::MicroServer multiplex_protocol(
      &pool, &fdcan_micro_server,
      []() {
        multiplex::MicroServer::Options options;
        options.max_tunnel_streams = 3;
        return options;
      }());

  // micro::AsyncStream* serial = multiplex_protocol.MakeTunnel(1);

  // micro::AsyncExclusive<micro::AsyncWriteStream> write_stream(serial);

  micro::EventQueue event_queue;
  micro::StreamPipe pipe{event_queue.MakePoster()};
  micro::AsyncExclusive<micro::AsyncWriteStream> write_stream{pipe.side_a()};

  micro::CommandManager command_manager(&pool, pipe.side_a(), &write_stream);
  char micro_output_buffer[2048] = {};
  micro::TelemetryManager telemetry_manager(
      &pool, &command_manager, &write_stream, micro_output_buffer);
  Stm32Flash flash_interface;
  micro::PersistentConfig persistent_config(
      pool, command_manager, flash_interface, micro_output_buffer);

  SystemInfo system_info(pool, telemetry_manager);
  FirmwareInfo firmware_info(pool, telemetry_manager,
                             kMoteusFirmwareVersion, MOTEUS_MODEL_NUMBER);
  Uuid uuid(persistent_config);
  ClockManager clock(&timer, persistent_config, command_manager);

  MoteusController moteus_controller(
      &pool, &persistent_config,
      &command_manager,
      &event_queue,
      pipe.side_b(),
      &telemetry_manager,
      &multiplex_protocol,
      &clock,
      &system_info,
      &timer,
      &firmware_info);

  BoardDebug board_debug(
      &pool, &command_manager, &telemetry_manager, &multiplex_protocol,
      moteus_controller.bldc_servo());

  persistent_config.Register("id", multiplex_protocol.config(), [](){});

  GitInfo git_info;
  telemetry_manager.Register("git", &git_info);

  CanConfig can_config, old_can_config;

  persistent_config.Register(
      "can", &can_config,
      [&can_config, &fdcan, &fdcan_micro_server, &old_can_config]() {
        // We only update our config if it has actually changed.
        // Re-initializing the CAN-FD controller can cause packets to
        // be lost, so don't do it unless actually necessary.
        if (can_config == old_can_config) {
          return;
        }
        old_can_config = can_config;

        FDCan::Filter filters[1] = {};
        filters[0].id1 = can_config.prefix << 16;
        filters[0].id2 = 0x1fff0000u;
        filters[0].mode = FDCan::FilterMode::kMask;
        filters[0].action = FDCan::FilterAction::kAccept;
        filters[0].type = FDCan::FilterType::kExtended;
        FDCan::FilterConfig filter_config;
        filter_config.begin = std::begin(filters);
        filter_config.end = std::end(filters);
        filter_config.global_std_action = FDCan::FilterAction::kAccept;
        filter_config.global_ext_action = FDCan::FilterAction::kReject;
        fdcan.ConfigureFilters(filter_config);

        fdcan_micro_server.SetPrefix(can_config.prefix);
      });

  persistent_config.Load();

  moteus_controller.Start();
  command_manager.AsyncStart();
  multiplex_protocol.Start(moteus_controller.multiplex_server());

  auto old_time = timer.read_us();

  for (;;) {
    if (rs485) {
      rs485->Poll();
    }
#if defined(TARGET_STM32G4)
    fdcan_micro_server.Poll();
#endif
    moteus_controller.Poll();
    multiplex_protocol.Poll();

    const auto new_time = timer.read_us();

    const auto delta_us = MillisecondTimer::subtract_us(new_time, old_time);
    if (delta_us >= 1000) {
      telemetry_manager.PollMillisecond();
      system_info.PollMillisecond();
      moteus_controller.PollMillisecond();
      board_debug.PollMillisecond();
      system_info.SetCanResetCount(fdcan_micro_server.can_reset_count());

      old_time += 1000;
    }

    SystemInfo::idle_count++;
  }

  return 0;
}

extern "C" {
  void abort() {
    mbed_die();
  }
}

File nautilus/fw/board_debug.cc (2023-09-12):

// Copyright 2018-2022 Josh Pieper, jjp@pobox.com.
//
// Licensed under the Apache License, Version 2.0 (the "License");
// you may not use this file except in compliance with the License.
// You may obtain a copy of the License at
//
//     http://www.apache.org/licenses/LICENSE-2.0
//
// Unless required by applicable law or agreed to in writing, software
// distributed under the License is distributed on an "AS IS" BASIS,
// WITHOUT WARRANTIES OR CONDITIONS OF ANY KIND, either express or implied.
// See the License for the specific language governing permissions and
// limitations under the License.

#include "fw/board_debug.h"

#include <cstdlib>
#include <functional>
#include <numeric>

#include "mbed.h"

#include "mjlib/base/inplace_function.h"
#include "mjlib/base/tokenizer.h"
#include "mjlib/base/visitor.h"

#include "fw/as5047.h"
#include "fw/bldc_servo.h"
#include "fw/bootloader.h"
#include "fw/drv8323.h"
#include "fw/moteus_hw.h"

namespace base = mjlib::base;
namespace micro = mjlib::micro;
namespace multiplex = mjlib::multiplex;

namespace moteus {
constexpr float kCalibrationStep = 0.002;
constexpr float kMaxCalPoleCount = 50.0f;

namespace {
void recurse(int count, base::inplace_function<void(int)> callback) {
  callback(count - 1);
}

bool ParseOptions(BldcServo::CommandData* command, base::Tokenizer* tokenizer,
                  const char* valid_options) {
  while (tokenizer->remaining().size()) {
    const auto token = tokenizer->next();
    // We accept optional arguments, each prefixed by a single
    // character.
    if (token.size() < 1) { continue; }
    const char option = token[0];
    if (::strchr(valid_options, option) == nullptr) {
      return false;
    }

    const float value = std::strtof(&token[1], nullptr);
    switch (option) {
      case 'p': {
        command->kp_scale = value;
        break;
      }
      case 'd': {
        command->kd_scale = value;
        break;
      }
      case 's': {
        command->stop_position = value;
        break;
      }
      case 'f': {
        command->feedforward_Nm = value;
        break;
      }
      case 't': {
        command->timeout_s = value;
        break;
      }
      case 'a': {
        command->accel_limit = value;
        break;
      }
      case 'v': {
        command->velocity_limit = value;
        break;
      }
      case 'o': {
        command->fixed_voltage_override = value;
        break;
      }
      default: {
        return false;
      }
    }
  }
  return true;
}
}

class BoardDebug::Impl {
 public:
  struct HistogramSource;

  Impl(micro::Pool* pool,
       micro::CommandManager* command_manager,
       micro::TelemetryManager* telemetry_manager,
       multiplex::MicroServer* multiplex_protocol,
       BldcServo* bldc_servo)
      : multiplex_protocol_(multiplex_protocol),
        bldc_(bldc_servo) {
    command_manager->Register(
        "d", std::bind(&Impl::HandleCommand, this,
                       std::placeholders::_1, std::placeholders::_2));

    data_update_ = telemetry_manager->Register("board_debug", &data_);
  }

  void PollMillisecond() {
    if (motor_cal_mode_ != kNoMotorCal) {
      DoCalibration();
    }
    if (histogram_active_) {
      DoHistogram();
    }
  }

  bool ParseHistogramChannel(HistogramSource* source, const std::string_view& spec) {
    // The format of this specification is a single character source:
    //
    //  t - electrical theta
    //  c - compensated
    //  f - filtered
    //  o - offset
    //  r - raw
    //  v - pll output velocity
    //  ... etc ...
    //
    // followed by an optional single digit to specify the encoder
    // channel, and then an optional list of non-digit flags:
    //
    //  d - derivative

    source->derivative = false;

    if (spec.size() < 2) { return true; }
    switch (spec[1]) {
      case 't': {
        source->type = HistogramSource::kElectricalTheta;
        break;
      }
      case 'c': {
        source->type = HistogramSource::kEncoderCompensated;
        break;
      }
      case 'f': {
        source->type = HistogramSource::kEncoderFiltered;
        break;
      }
      case 'o': {
        source->type = HistogramSource::kEncoderOffset;
        break;
      }
      case 'r': {
        source->type = HistogramSource::kEncoderRaw;
        break;
      }
      case 'v': {
        source->type = HistogramSource::kEncoderVelocity;
        break;
      }
      case 'd': {
        source->type = HistogramSource::kCurrentD;
        break;
      }
      case 'q': {
        source->type = HistogramSource::kCurrentQ;
        break;
      }
      case 'e': {
        source->type = HistogramSource::kPositionError;
        break;
      }
      case 'E': {
        source->type = HistogramSource::kPositionErrorRate;
        break;
      }
      default: {
        return true;
      }
    }

    size_t offset = 2;

    if (spec.size() <= offset) { return false; }
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

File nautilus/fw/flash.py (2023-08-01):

#!/usr/bin/python3

# Copyright 2021 Josh Pieper, jjp@pobox.com.
#
# Licensed under the Apache License, Version 2.0 (the "License");
# you may not use this file except in compliance with the License.
# You may obtain a copy of the License at
#
#     http://www.apache.org/licenses/LICENSE-2.0
#
# Unless required by applicable law or agreed to in writing, software
# distributed under the License is distributed on an "AS IS" BASIS,
# WITHOUT WARRANTIES OR CONDITIONS OF ANY KIND, either express or implied.
# See the License for the specific language governing permissions and
# limitations under the License.

import argparse
import platform
import subprocess
import sys
import tempfile


BINPREFIX = '' if platform.machine().startswith('arm') else 'arm-none-eabi-'

OBJCOPY = BINPREFIX + 'objcopy'
OPENOCD = 'openocd -f interface/stlink.cfg -f target/stm32g4x.cfg '


def main():
    parser = argparse.ArgumentParser()
    parser.add_argument('--erase', action='store_true')
    parser.add_argument(
        'elffile', nargs='?',
        default='bazel-out/stm32g4-opt/bin/fw/nautilus.elf')
    parser.add_argument(
        'bootloader', nargs='?',
        default='bazel-out/stm32g4-opt/bin/fw/can_bootloader.elf')

    args = parser.parse_args()

    tmpdir = tempfile.TemporaryDirectory()

    moteus_elffile = args.elffile
    bootloader_elffile = args.bootloader

    subprocess.check_call(
        f'{OBJCOPY} -Obinary ' +
        f'-j .isr_vector ' +
        f'{moteus_elffile} {tmpdir.name}/out.08000000.bin',
        shell=True)

    subprocess.check_call(
        f'{OBJCOPY} -Obinary ' +
        f'-j .text -j .ARM.extab -j .ARM.exidx -j .data -j .bss ' +
        f'{bootloader_elffile} {tmpdir.name}/out.0800c000.bin',
        shell=True)

    subprocess.check_call(
        f'{OBJCOPY} -Obinary ' +
        f'-j .text -j .ARM.extab -j .ARM.exidx -j .data -j .ccmram -j .bss ' +
        f'{moteus_elffile} {tmpdir.name}/out.08010000.bin',
        shell=True)

    subprocess.check_call(
        f'{OPENOCD} -c "init" ' +
        f'-c "reset_config none separate; ' +
        f' halt; ' +
        (f' stm32l4x mass_erase 0; ' if args.erase else '') +
        f' program {tmpdir.name}/out.08000000.bin verify 0x8000000; ' +
        f' program {tmpdir.name}/out.0800c000.bin verify 0x800c000; ' +
        f' program {tmpdir.name}/out.08010000.bin verify  ' +
        f' reset exit 0x08010000"',
        shell=True)


if __name__ == '__main__':
    main()

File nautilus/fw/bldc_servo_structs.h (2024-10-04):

// Copyright 2018-2022 Josh Pieper, jjp@pobox.com.
//
// Licensed under the Apache License, Version 2.0 (the "License");
// you may not use this file except in compliance with the License.
// You may obtain a copy of the License at
//
//     http://www.apache.org/licenses/LICENSE-2.0
//
// Unless required by applicable law or agreed to in writing, software
// distributed under the License is distributed on an "AS IS" BASIS,
// WITHOUT WARRANTIES OR CONDITIONS OF ANY KIND, either express or implied.
// See the License for the specific language governing permissions and
// limitations under the License.

#pragma once

#include <cstdint>
#include <optional>

#include "mjlib/base/visitor.h"

#include "fw/error.h"
#include "fw/measured_hw_rev.h"
#include "fw/pid.h"
#include "fw/simple_pi.h"

namespace moteus {

struct Vec3 {
  float a = 0.0f;
  float b = 0.0f;
  float c = 0.0f;

  template <typename Archive>
  void Serialize(Archive* ar) {
    ar->Visit(MJ_NVP(a));
    ar->Visit(MJ_NVP(b));
    ar->Visit(MJ_NVP(c));
  }
};

enum BldcServoMode {
  // In this mode, the entire motor driver will be disabled.
  //
  // When exiting this state, the current offset will be
  // recalibrated.
  kStopped = 0,

  // This stage cannot be commanded directly, but will be entered
  // upon any fault.  Here, the motor driver remains enabled, but
  // the output stage power is removed.  The only valid transition
  // from this state is to kStopped.
  kFault = 1,

  // This mode may not be commanded directly.  It is used when
  // transitioning from kStopped to another mode.
  kEnabling = 2,

  // This mode may not be commanded directly, but is used when
  // transitioning from kStopped to another mode.
  kCalibrating = 3,

  // This mode may not be commanded directly, but is used when
  // transitioning from kStopped to another mode.
  kCalibrationComplete = 4,

  // Directly control the PWM of all 3 phases.
  kPwm = 5,

  // Control the voltage of all three phases
  kVoltage = 6,

  // Control the phase and voltage magnitude
  kVoltageFoc = 7,

  // Control d and q voltage
  kVoltageDq = 8,

  // Control d and q current
  kCurrent = 9,

  // Control absolute position
  kPosition = 10,

  // This state can be commanded directly, and will also be entered
  // automatically upon a watchdog timeout from kPosition.  When in
  // this state, the controller will apply the selected fallback
  // control mode.
  //
  // The only way to exit this state is through a stop command.
  kPositionTimeout = 11,

  // Control to zero velocity through a derivative only version of
  // the position mode.
  kZeroVelocity = 12,

  // This applies the PID controller only to stay within a
  // particular position region, and applies 0 torque when within
  // that region.
  kStayWithinBounds = 13,

  // This mode applies a fixed voltage square waveform in the D axis
  // in order to measure inductance assuming a motor with
  // approximately equal D/Q axis inductances.
  kMeasureInductance = 14,

  // All phases are pulled to ground.
  kBrake = 15,

  // PI-based velocity control
  kVelocity = 16,

  kNumModes,
};

struct BldcServoStatus {
  BldcServoMode mode = kStopped;
  errc fault = errc::kSuccess;

  uint16_t adc_cur1_raw = 0;
  uint16_t adc_cur2_raw = 0;
  uint16_t adc_cur3_raw = 0;
  uint16_t adc_voltage_sense_raw = 0;
  uint16_t adc_fet_temp_raw = 0;
  uint16_t adc_motor_temp_raw = 0;

  uint16_t adc_cur1_offset = 2048;
  uint16_t adc_cur2_offset = 2048;
  uint16_t adc_cur3_offset = 2048;

  float cur1_A = 0.0f;
  float cur2_A = 0.0f;
  float cur3_A = 0.0f;

  float bus_V = 0.0f;
  float filt_bus_V = std::numeric_limits<float>::quiet_NaN();
  float filt_1ms_bus_V = std::numeric_limits<float>::quiet_NaN();
  float fet_temp_C = 0.0f;
  float filt_fet_temp_C = std::numeric_limits<float>::quiet_NaN();
  float motor_temp_C = 0.0f;
  float filt_motor_temp_C = std::numeric_limits<float>::quiet_NaN();

  float d_A = 0.0f;
  float q_A = 0.0f;

  float position = 0.0f;
  float velocity = 0.0f;
  float torque_Nm = 0.0f;

  float velocity_filt = 0.0f;

  SimplePI::State pid_d;
  SimplePI::State pid_q;
  PID::State pid_position;
  PID::State pid_velocity;

  // This is measured in the same units as MotorPosition's integral
  // units, which is 48 bits to represent 1.0 unit of output
  // revolution.
  std::optional<int64_t> control_position_raw;
  float control_position = std::numeric_limits<float>::quiet_NaN();
  std::optional<float> control_velocity;
  float position_to_set = std::numeric_limits<float>::quiet_NaN();
  float timeout_s = 0.0;
  bool trajectory_done = false;

  float torque_error_Nm = 0.0f;

  float sin = 0.0f;
  float cos = 0.0f;
  uint16_t cooldown_count = 0;
  uint32_t final_timer = 0;
  uint32_t total_timer = 0;

  float meas_ind_old_d_A = 0.0f;
  int8_t meas_ind_phase = 0;
  float meas_ind_integrator = 0.0f;
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

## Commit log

2023-06-18 Start of Nautilus project
    Migrate schematic from Eagle to Kicad.
    Schematic modifications: introduce CSD88599Q5DC, remove CAN port.
    Tentative PCB layout.
    [nautilus.kicad_pcb, nautilus.kicad_sch, outline.dxf]
2023-07-09 First PCB layout, before DRC.
    [nautilus.kicad_pcb, nautilus.kicad_sch]
2023-07-09 First PCB design passing DRC
    [nautilus.kicad_pcb, nautilus.kicad_sch]
2023-07-14 Cleanup PCB before order
    [nautilus.kicad_pcb, nautilus.kicad_sch, outline.dxf]
2023-07-16 Minor PCB update
    [nautilus.kicad_pcb, nautilus.kicad_sch]
2023-07-16 [Hardware] First prototype order
    [nautilus.kicad_pcb, nautilus.kicad_sch]
2023-08-01 Update pin mapping to be compatible with nautilus
2023-08-03 POC of spi communication
2023-08-03 POC of frame transfer. RX works, TX live updates work, but the TX buffer is not flushed...
2023-08-04 Clear SPI Tx buffer on SS high
2023-08-27 First prototype assembly
    - [hw] Fix reverse XT-30 connector in PCB
    - [sw] Add led blink to SPI communication
    - [sw] Add note about using SPI1 mode only (other modes don't work)
    [nautilus.kicad_pcb, nautilus.kicad_sch]
2023-09-02 Add dummy SPI read function
2023-09-05 Start filling SPI read function
2023-09-07 SPI: add temperature reading
    [nautilus.kicad_pcb]
2023-09-09 Aux port configuration: hard-code AS5048 as secondary sensor and send reading to SPI
2023-09-09 Add I2C disconnect detection
2023-09-09 Hard-code default motor config
2023-09-12 Begin support for write command. Assign true debug role to the onboard LEDs. Fix some incorrect read instructions.
    [board_debug.cc, moteus.cc, moteus_hw.cc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]
2023-09-19 Add RaspberryPi driver & GUI. Begining of work on getting the commutation working on the motor.
2023-09-22 Add DRV debug register to SPI register list.
2023-09-22 [NautilusGUI] Rework register list.
    [Commutation.cpp, NautilusDriver.cpp, NautilusGUI.cpp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]
2023-09-27 [NautilusGUI] Add code for servo control, with plotting using Teleplot.
2023-09-29 Working POC, in position and current mode.
    - Improve commutation algorithm by performing gradual motion.
    - Remove position limit and current derate from driver.
    - Add possibility to update control gains from SPI.
    Note: commutation parameters are currently not stored to persistent memory.
2023-09-30 Add button to save the configuration to the flash memory.
2023-09-30 NautilusGUI: code cleanup, fix termination segfault.
    [NautilusDriver.cpp, NautilusGUI.cpp, NautilusGUI.h]
2023-10-03 [fw] Add velocity control mode. Configure default parameters for the RMDXV2 motor.
    Bugfixes and improvement to the GUI.
    [Commutation.cpp, NautilusGUI.cpp, NautilusRegisters.h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]
2023-10-05 [NautilusGUI] Various improvements
    - Keep spi port open
    - Monitor motor state, and stop generating signal on error
    [NautilusDriver.cpp, NautilusGUI.cpp, NautilusGUI.h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]
2023-10-07 Optimize SPI timing: clock speed up to 8MHz have been successfully tested.
2023-10-08 [Hardware] PCB V2: new layout, using LQFP package for microcontroller.
    [nautilus.kicad_pcb, nautilus.kicad_sch]
2023-10-09 [fw] Return motor integrated position instead of encoder single-turn value.
    Position and velocity target now in rad.
    Update control gains.
2023-10-29 [Hardware] V2 board order
    [nautilus.kicad_pcb, nautilus.kicad_sch]
2023-12-21 Minor PCB fixup
    [nautilus.kicad_pcb, nautilus.kicad_sch]
2023-12-25 Add missing build files. Update resistor value for led brightness.
    [nautilus.kicad_sch]
2023-12-25 Various firmware fixup
    - Checksum: use 1 complement
    - Add firmware version register
    - Improve 'store to persistent config' option: though it only works once then crashes,
    at least the new version compiles using 'vanilla' external lib version
    [NautilusDriver.cpp, NautilusGUI.cpp, NautilusRegisters.h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]
2023-12-25 Reduce position pll filter frequency to 100Hz. Add picture of PCB prototype.
2024-01-06 [NautilusGui] Add sendInvalidCommand to test feature & red led
2024-08-26 Update current sense filtering to 14kHz to avoid aliasing.
    [nautilus.kicad_pcb, nautilus.kicad_sch]
2024-10-04 Update control gains to match new current filter. Make number of poles writable.
